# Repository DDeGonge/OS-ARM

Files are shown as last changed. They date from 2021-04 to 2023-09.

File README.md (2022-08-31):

# OS-ARM
An open-sourced, low cost, high performance 3D printed 6-axis robotic arm. The main goals of this project are
- Smooth, repeatable motion
- ~1kg payload
- ~500mm range
- Low cost (<$500 in materials)
- Easy to reproduce (only requiring an FDM printer and basic hand tools)
- Beautiful
- Easy to control

This arm is not industrial and it will not be fast, but that is not my goal. But it will hopefully be a very nice looking arm fully capable of 6dof motion, cheap enough to keep it accessable but capable enough to actually do something (aka carry more than a 50g payload). This is not your typical RC servo arm. It's gonna be epic.

Developemnt will likely take multiple years. This repo will be a work in progress until stated otherwise. Use these files at your own risk!

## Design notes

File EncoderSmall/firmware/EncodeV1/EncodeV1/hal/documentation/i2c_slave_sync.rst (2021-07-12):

============================
I2C Slave synchronous driver
============================

I2C (Inter-Integrated Circuit) is a two wire serial interface commonly used
for on-board low-speed bi-directional communication between controllers and
peripherals. There can be several slave devices on I2C bus.
I2C uses only two bidirectional open-drain lines, usually designated SDA
(Serial Data Line) and SCL (Serial Clock Line), with pull up resistors.

I2C Modes (standard mode/fastmode+/highspeed mode) can only be selected in
Atmel Start.

Features
--------

	* I2C Slave support
	* Initialization and de-initialization
	* Enabling and disabling
	* 10- and 7- bit addressing
	* Setting slave address
	* I2C Modes supported
	       +----------------------+-------------------+
	       |* Standard/Fast mode  | (SCL: 1 - 100kHz) |
	       +----------------------+-------------------+
	       |* Fastmode+           | (SCL: 1 - 1000kHz)|
	       +----------------------+-------------------+
	       |* Highspeed mode      | (SCL: 1 - 3400kHz)|
	       +----------------------+-------------------+

Applications
------------

* Sensors, device to device communication, memory.

Dependencies
------------

* I2C Slave capable hardware

Concurrency
-----------

N/A

Limitations
-----------

* System Management Bus (SMBus) not supported.
* Power Management Bus (PMBus) not supported.

Known issues and workarounds
----------------------------

N/A

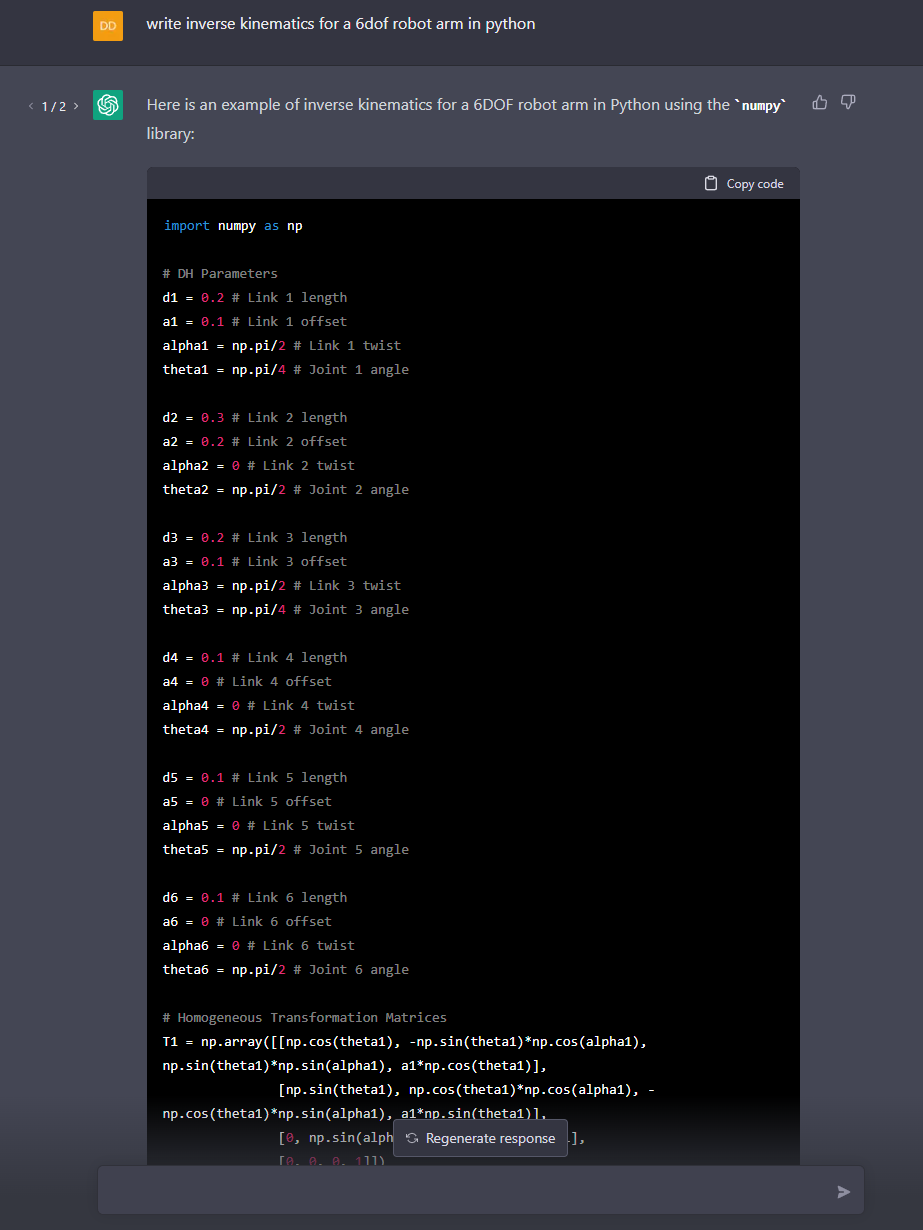
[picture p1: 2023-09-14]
firmware/chatgpt.png

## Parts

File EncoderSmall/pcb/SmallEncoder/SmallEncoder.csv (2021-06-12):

Id | Designator | Package | Quantity | Designation | Supplier and ref
1 | J3 | PinHeader_1x05_P2.54mm_Vertical | 1 | Conn_01x05
2 | C5,C4,C3 | C_0603_1608Metric | 3 | 100nF
3 | H3,H2,H1 | MountingHole_2.7mm_M2.5_DIN965_Pad | 3 | MountingHole_Pad
4 | R2 | R_0603_1608Metric | 1 | 174
5 | R1 | R_0603_1608Metric | 1 | 10k
6 | C2 | C_0603_1608Metric | 1 | 1uF
7 | C1 | C_0805_2012Metric | 1 | 10uF
8 | U3 | SOT-96-1 | 1 | KMZ49
9 | J2,J1 | PinHeader_1x04_P2.54mm_Horizontal | 2 | Conn_01x04
10 | U2 | SOT-23-5 | 1 | AP2112K-3.3
11 | S1 | KMR421GULCLFS | 1 | KMR243GLFG
12 | IC1 | QFN50P500X500X100-33N-D | 1 | ATSAMD21E15B

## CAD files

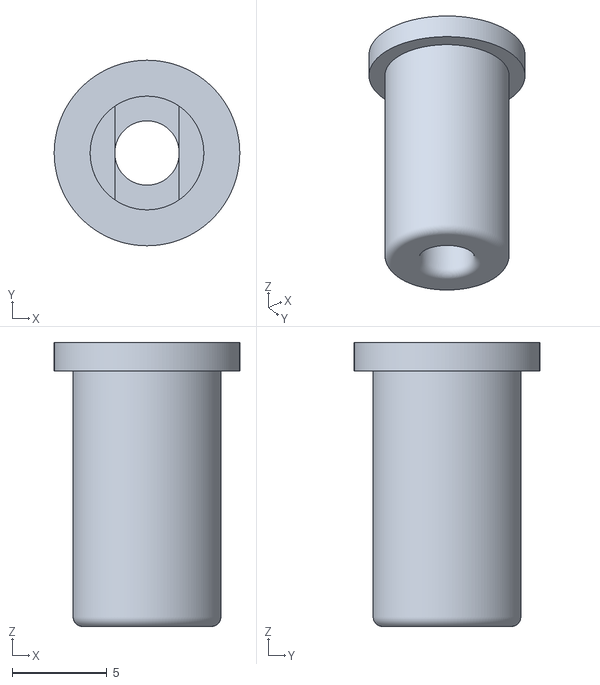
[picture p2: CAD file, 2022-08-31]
cad/HarmonicDrive75mm V2/HD_BearingShaft2.stl
9.80 x 9.80 x 15.0

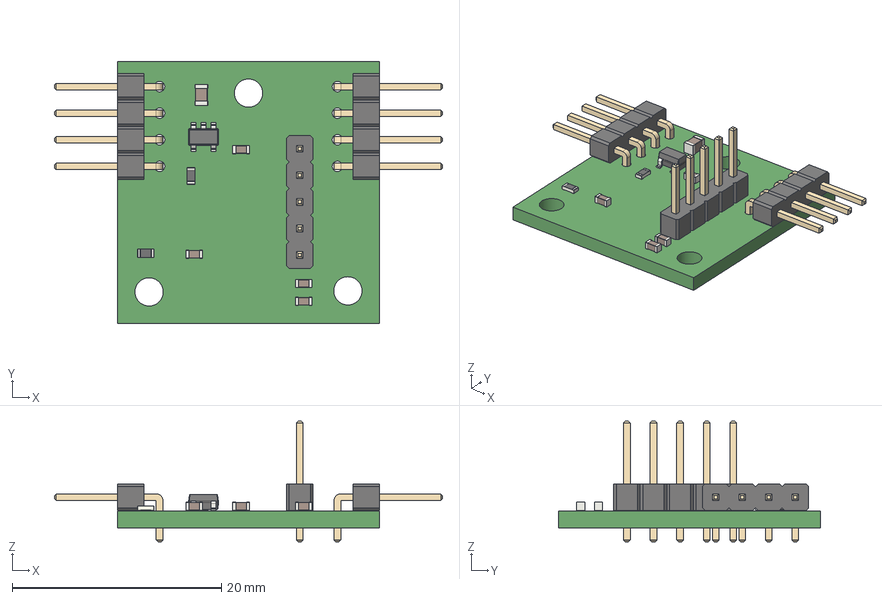
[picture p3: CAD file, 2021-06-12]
EncoderSmall/pcb/SmallEncoder/SmallEncoder.step
37.1 x 25.0 x 11.5 mm

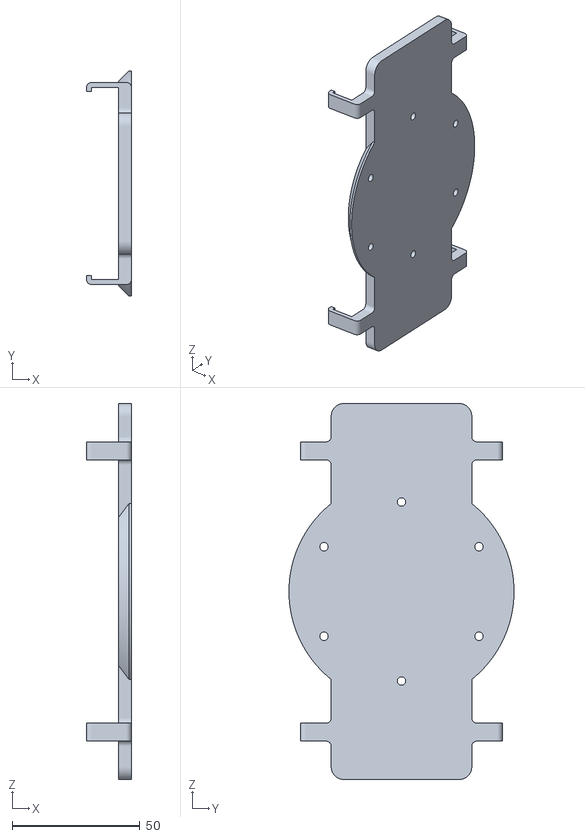
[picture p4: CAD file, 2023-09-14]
cad/FirstDraft/PhoneHOldER.stl
17.6 x 88.0 x 147.0

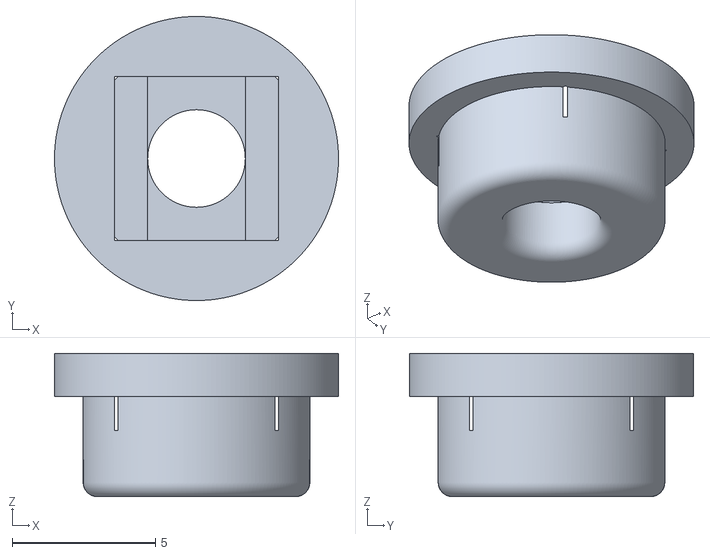
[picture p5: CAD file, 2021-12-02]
cad/HarmonicDrive75mm V2/HD_BearingShaft1.stl
9.90 x 9.90 x 5.00

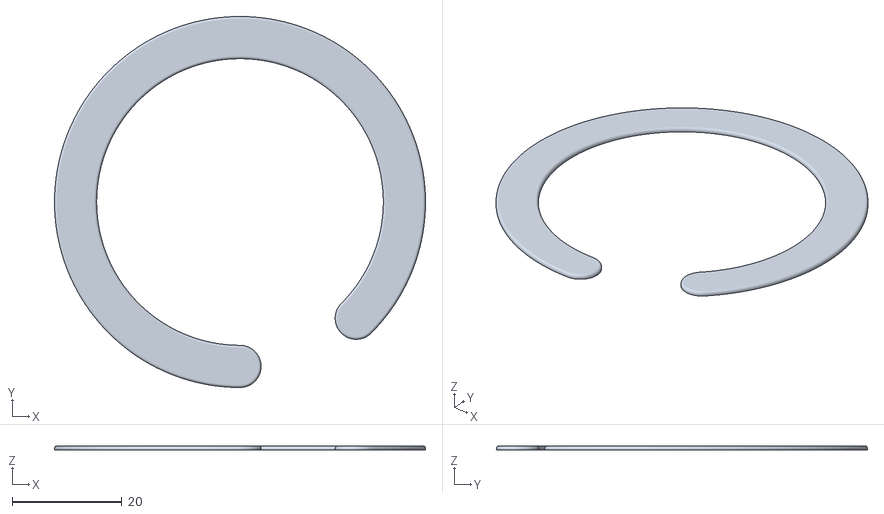
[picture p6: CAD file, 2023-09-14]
cad/FirstDraft/LogoCoverThin.stl
67.7 x 67.7 x 0.8

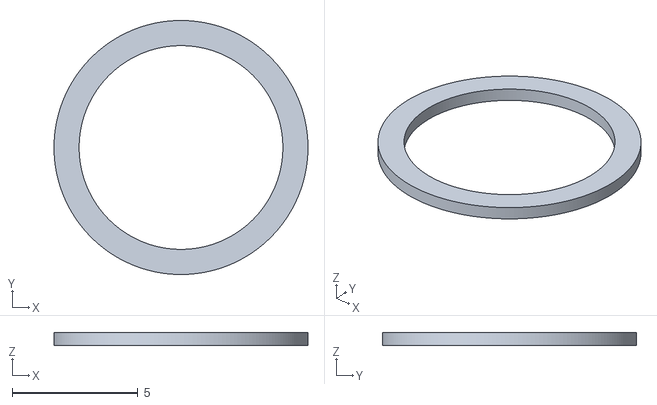
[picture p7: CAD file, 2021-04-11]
cad/HarmonicDrive75mm V2/HD_bearingshim.stl
10.1 x 10.1 x 0.5

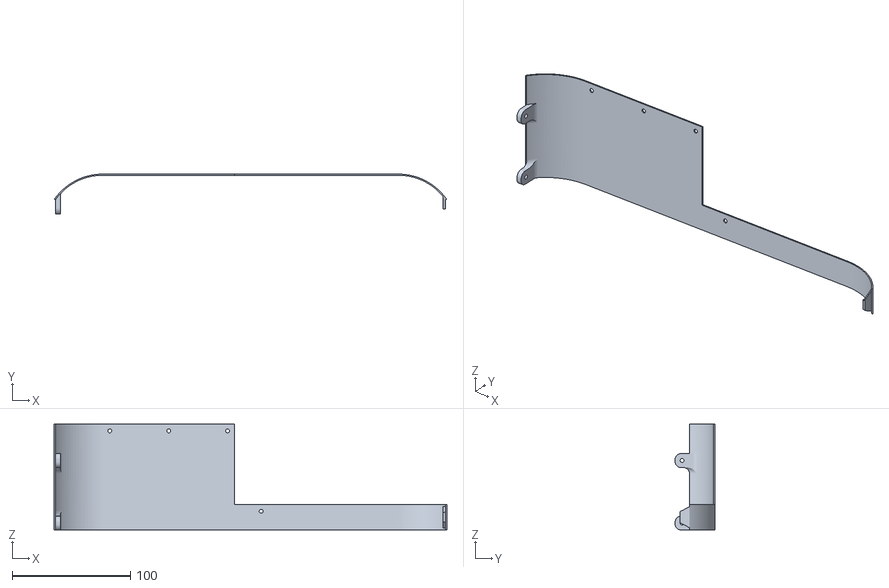
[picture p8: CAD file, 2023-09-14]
cad/FirstDraft/Link1CoverA.stl
332.4 x 33.7 x 89.6

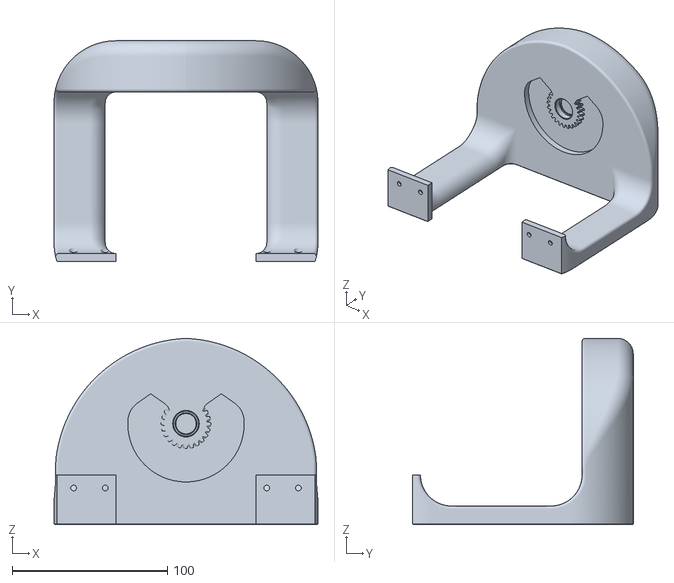
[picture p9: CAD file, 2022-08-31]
cad/FirstDraft/J1_NewBase.stl
170.0 x 142.0 x 119.9

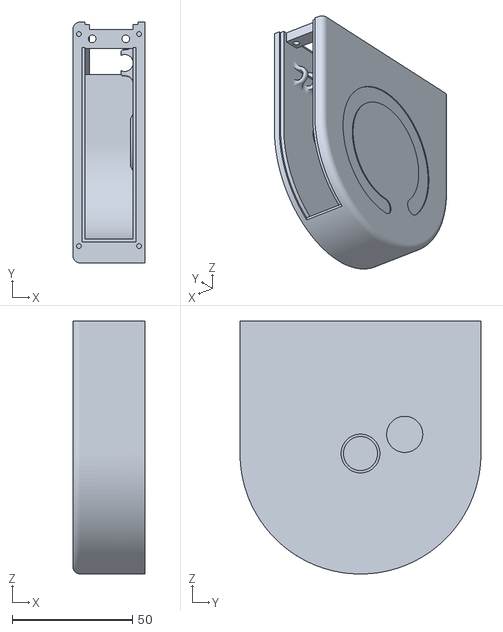
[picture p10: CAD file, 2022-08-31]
cad/FirstDraft/Link1c.stl
30.0 x 100.0 x 105.0

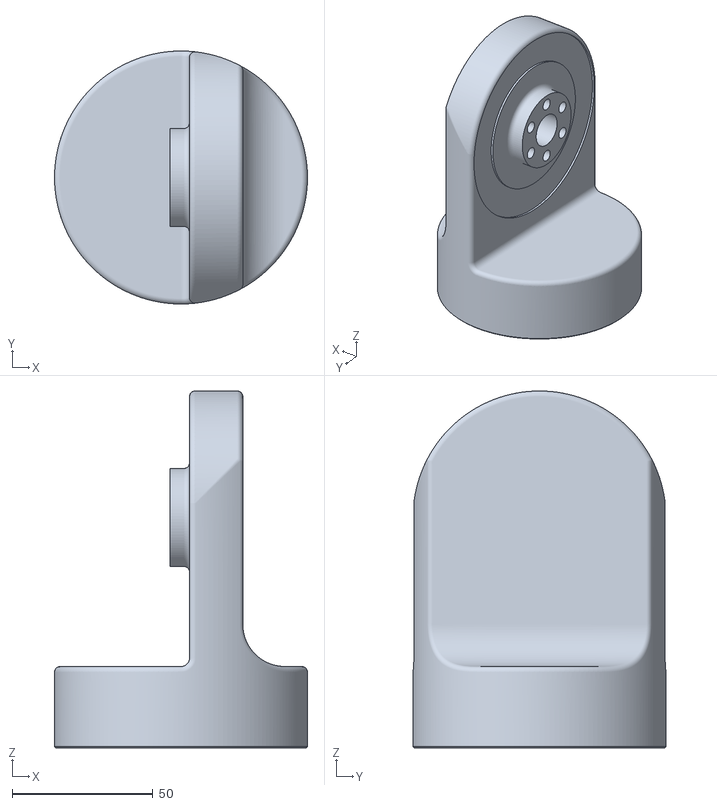
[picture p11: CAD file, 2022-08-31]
cad/FirstDraft/Link3.stl
90.0 x 90.0 x 127.0

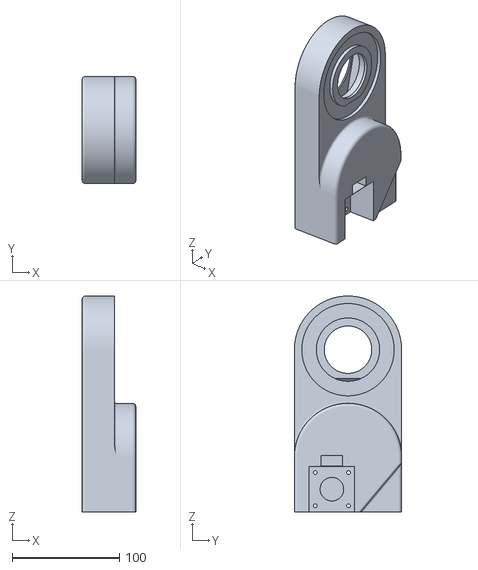
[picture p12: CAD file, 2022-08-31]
cad/FirstDraft/Link2B.stl
50.0 x 100.0 x 201.2

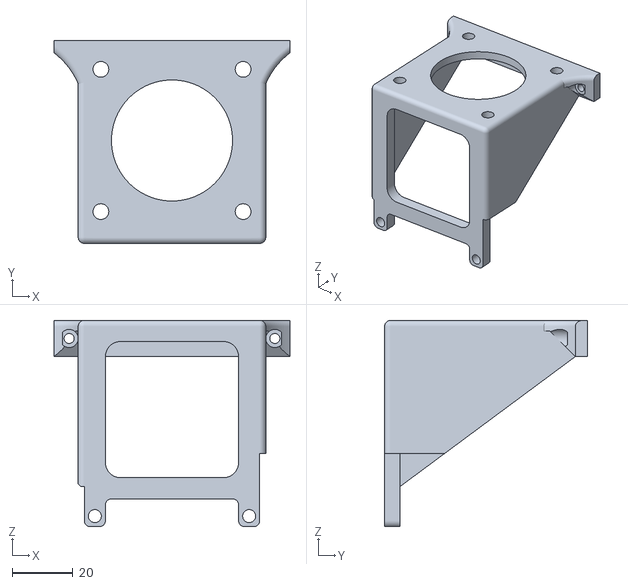
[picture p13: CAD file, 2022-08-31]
cad/FirstDraft/J2MotorBracket.stl
78.0 x 67.0 x 68.2

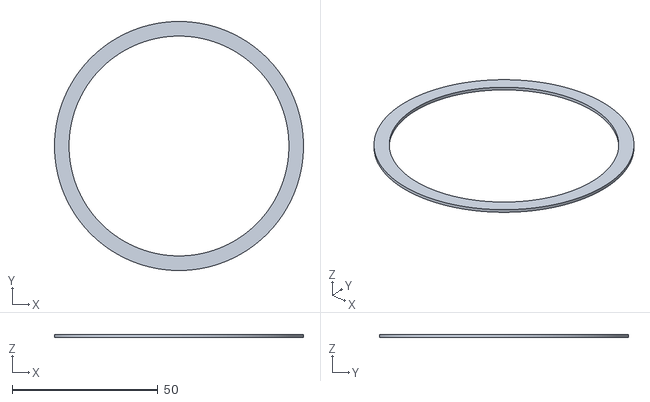
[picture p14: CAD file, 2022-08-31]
cad/FirstDraft/HDSpacer.stl
85.3 x 85.3 x 1.00

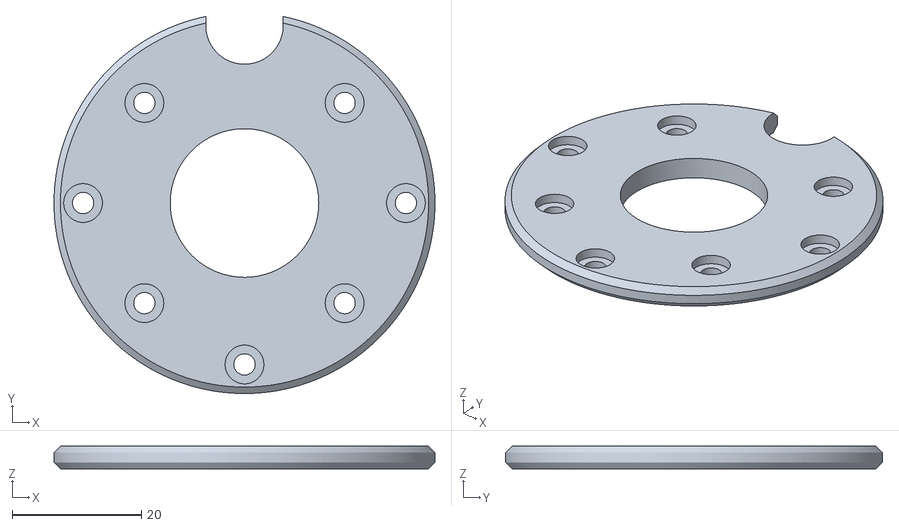
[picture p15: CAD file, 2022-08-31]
cad/FirstDraft/WristMotorPlate.stl
59.0 x 58.4 x 3.50

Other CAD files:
cad/FirstDraft/Link2_SpinCover.stl
cad/FirstDraft/Link2_FlatCover.stl
cad/FirstDraft/LogoCover.stl
cad/FirstDraft/TrainingTarget.stl
cad/FirstDraft/Base.ipt
cad/FirstDraft/Base.stl
cad/FirstDraft/BaseWasher.ipt
cad/FirstDraft/BaseWasher.stl
cad/FirstDraft/CamBracket.ipt
cad/FirstDraft/CamMount.ipt
cad/FirstDraft/Deskcap.ipt
cad/FirstDraft/Deskcap.stl
cad/FirstDraft/DraftAssembly.iam
cad/FirstDraft/DraftAssembly/Design Accelerator/OldVersions/Spur Gears1.0001.iam
cad/FirstDraft/DraftAssembly/Design Accelerator/OldVersions/Spur Gears2.0001.iam
cad/FirstDraft/DraftAssembly/Design Accelerator/Spur Gear21.ipt
cad/FirstDraft/DraftAssembly/Design Accelerator/Spur Gears1.iam
cad/FirstDraft/DraftAssembly/Design Accelerator/Spur Gears2.iam
cad/FirstDraft/EncoderSketch.ipt
cad/FirstDraft/EncoderV1/COMPOUND.ipt
cad/FirstDraft/EncoderV1/C_0603_1608Metric.iam
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

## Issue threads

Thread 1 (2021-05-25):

Slicer parameters and print material

3mrrrx, 2021-05-25:
Kindly add some information about the used slicer and parameters as well as the material that could be used for each part in read me.

DDeGonge, 2021-06-05:
Slicing and material is entirely up to you. I used PLA, PETG or ABS would likely offer slightly better performance, nylon the best. 30% or higher infill should be ok.

Closed 2021-06-05.

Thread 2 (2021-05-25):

bill of materials for the non-3D printed parts

3mrrrx, 2021-05-25:
bill of materials for the non-3D printed parts would be very very very very helpful recreate and try the project.

thank you!

DDeGonge, 2021-06-05:
I'll be filling in the BOM as I work on the project, apologies for the delay. The harmonic drive uses 608 and 688 bearings, plus some M3 square nuts and M3 bolts (I believe 20mm length for the bearing posts). But I will be uploading a full BOM in the next few weeks!

jlogan223, 2023-02-26:
Is there any update on this?

DDeGonge, 2023-03-10:
> Is there any update on this?

Hey sorry about that. I'm currently reworking the design from scratch so this design of the full arm is frozen. I plan to have a full BOM with the redesign which will be in Onshape so it is more accessible. But I don't have any idea of the full BOM for this iteration so if you want to build any part of it, you will need to open the cad and work out fasteners from that. Bearings are already included. And some heat stake inserts are used in the larger shallow holes where there's a screw but no obvious nut.

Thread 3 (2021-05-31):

lever at power off

michael-thompson-32214, 2021-05-31:
curious.
when the power is turned off.
does the lever arm rotate clock wise or counter clock wise easily

DDeGonge, 2021-06-05:
It does not, strain wave gearboxes usually can not be back-driven. This gearbox will hold its position when it is powered off.

Closed 2021-06-05.

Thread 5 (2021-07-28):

what program is required to edit the files?

bryanerayner, 2021-07-28:
Novice question here - what program is required to edit these files? Are there any free / freemium programs which would allow access?

Not asking you to change the way you work - thanks so much for opening this up! But a simple programmer like myself with no CAD experience would just like to know how to cut his teeth.

Thanks!

DDeGonge, 2021-08-01:
Autodesk Inventor is required to access the source files, though I have uploaded STEP files for the harmonic drive assembly and will for the full arm once it is in a stable place. STEP files can be opened and edited by most cad programs including some free ones, though editing features is not as easy as using Autodesk Inventor.

Closed 2021-08-01.

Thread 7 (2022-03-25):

Motor coupling missing?

Eufrades, 2022-03-25:
Hello DDeGonge,
I like the design of your 75mm harmonic drive, and I want to use it to drive a sand feeder for my sand spreader on the back of my garden tractor.
I printed all of the .stl parts from the V2 folder, but the wave generator is not the same as the one in your video, its obviously a newer version. There appears to be a coupling of some sort that goes between the wave generator and the motor. I've looked to see if I have missed a file, but I can't find it. Is that hiding somewhere?

Thanks for all of your work,
Eufrades

gandrewstone, 2022-03-28:
I think its meant to take a 20T GT2 timing belt pulley with the top flange popped off (based on a comment to the video here: https://www.youtube.com/watch?v=Emvo3bLT-Z4&t=16s).  I've got a stepper out of an old epson printer with a pulley that seems to match the wave generator... except I'm not sure because not sure how to pop the top flange off (blowtorch maybe?)

Since you are active, I have a question for you... have you figured out how the top housing is secured?  Seems to me like it would just fall off

gandrewstone, 2022-03-29:
Thats a good thought about the large bearing.  I bought one so in a few days I'll be able to tell.  That probably won't work for me either.  I was thinking of using it for a SCARA robot, so there will be force parallel to the motor shaft.  Maybe a stationary lid with a thrust bearing between will work for me, or something through the axle... What is your application?

Anyway the gear i had didnt actually fit, off by 2mm, so i made a bigger hole.  I also had elephant feet on my flex spline, so i fixed that by raising the teeth a tiny bit off the bed and printing with no supports.  I also put the skirt on the inside only.  I can give you the bkender models if you want.

gandrewstone, 2022-03-29:
What about the 688 bearings?  I think that they were originally on the motor shaft, but are not needed in the V2 design.

Eufrades, 2022-03-29:
I think you're right on the bearings, it doesn't look like they're needed anymore. As long ans the motor is mounted solidly to the bottom housing.
My application isn't typical for this type of gearbox, I just needed something with a really big speed reduction in a small package. I'm planning to use it on a sand spreader on the back of my atv. There is a motor there that already spins the spreader, but I wanted to use the same motor to really slowly turn an agitator in the sand hopper because the sand keeps getting hung up in there.
I appreciate the offer of your files, but I think I'm going to modify this quite a bit more to slow it down even more for me.

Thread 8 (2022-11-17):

Reduction ratio

Okosai, 2022-11-17:
So, i am modifying v2 harmonic drive (for my motorised telescope mount) and i am trying to figure out what is actual rediction ratio for it. As far as i understood one of the rings has 70 teeth and 68 another, meanwhile spline has 66 teeth... could not find any info on that.
Thanks

KoehIl180151, 2023-01-27:
I would also need this information.
I tried to calculate it myself with the steps per rev and i got 1:29 but in testing it didn't quite work out.

bfra2373, 2023-01-27:
Looking at [wiki](https://en.wikipedia.org/wiki/Strain_wave_gearing) You should see that the  ratio is
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
or For example, if there are 202 teeth on the circular spline and 200 on the flex spline, the reduction ratio is (200 − 202)/200 = −0.01

DDeGonge, 2023-01-27:
Because my harmonic drive is designed different than the standard, the formula above needs slight modification.

The number of teeth in my "flex spline" is irrelevant, instead what matters is the number of teeth on the input (circle spline equivalent) vs output (flex spline equivalent) sides of the housing. So the formula would be (68 - 70) / 68, which gives a reduction of **34:1**. Note this equation results in a negative number, which means the output spins the opposite direction of the input.

Closed 2023-01-27.

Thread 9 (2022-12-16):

Export to other cad formats

bit-wrangler, 2022-12-16:
Hey, do you mind exporting the gearbox design to solidworks or STEP? I guess I'm working with some pretty old CAD as it's erroring out trying to import the ipt/iam files.

DDeGonge, 2023-09-14:
Apologies for not seeing this sooner, done now

Closed 2023-09-14.

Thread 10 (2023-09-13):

Different Modules Gear Meshing

Archav, 2023-09-13:
Can someone explain how the gears mesh? I'm currently working on my own harmonic drive with different gear ratio and am using this as a reference on how to go about printing it.
Looking at the CAD files the ring gear and the flex spline have 70 and 68 teeth. When creating the gear in Inventors Spur Gear generator there is too much overlap in teeth to allow the flex spline to mesh. This design seems to be using two different gear modules to create more of a gap. has anyone encountered any issues with gear meshing or tips to know while printing?
Thanks in advance.

DDeGonge, 2023-09-14:
The teeth were designed from scratch in my design, and the tooth was patterned 2 additional times over the same circumference. You may not be able to do this if you're using a script or add-on to generate the gear teeth. Additionally, the standard involute gear profile is probably not the optimal shape for this time of gearbox. So making teeth from scratch would give more room for improving efficiency and thus power output.

Closed 2023-09-14.

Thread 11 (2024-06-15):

Printer Material and Settings

cmagorian, 2024-06-15:
Hey! Nice work on this, just found your video which brought me back here.

What print settings did you use across all the parts? Did you use a different filament for the FlexiSpine? If so, which one?

Thanks!
Chris

DDeGonge, 2025-02-11:
Sorry late reply - I used PLA but would recommend PETG be used for the flex spline. More tensile strength is generally better (hence PLA) but the flex spline needs better fatigue resistance. CF filled may help too but those plastics are more abrasive so lifetime might be reduced. I haven't tried using nylon filament but I suspect that would work very well for the flex spline as well. It may be too soft for the entire gearbox though depending on the blend.

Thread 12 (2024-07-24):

Upload SPT of the entire OS-ARM First Draft

cmagorian, 2024-07-24:
Hey!

Started using this at my own risk. I am mostly interested in just building out parts of the arm for 4DOF: Waist, Shoulder, Elbow and Wrist (1 DOF). Any way you could upload an STP of the First Draft assembly? The parts are in here, but I don't see the thing put together. Those of us using Onshape can't import the IAM files.

Thanks!
Chris

DDeGonge, 2024-07-25:
Added under cad/FirstDraft/DraftAssembly.step

Closed 2024-07-25.

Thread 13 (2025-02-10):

Likely limitation to achieve 2x torque

spit40, 2025-02-10:
I have a motion platform for flight simulation. The motors are terrible though. They are windscreen wiper worm drives with loads of backlash. I’m thinking that a 3d printed strainwave motor could be the solution. It hink i’d need 2x to 3x torque though but am concerned that a stronger motor would simply result in mechanical failure probably on the toothed belt. Has anyone else tried to scale this up in torque?

DDeGonge, 2025-02-11:
I would definitely not recommend a 3D printed gearbox for loads that high. While this gearbox could probably operate at up to a 20Nm output, I have some hesitation about the lifetime. Even at 10Nm I wouldn't be surprised to start seeing fatigue failures after a few weeks under these loads.

If you need linear motion, using a cheap ball screw with a geared down input from a motor using a belt reduction would be a reliable way to hit very high output forces. If you need rotation, an off the shelf solution would be expensive but if you want it to last any amount of time it's either that, or likely a whole lot of engineering and trials before you hit a reliable solution.

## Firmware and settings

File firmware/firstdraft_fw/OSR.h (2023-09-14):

#include <Arduino.h>
#include <SPI.h>
#include <vector>
#include <iostream>

#define NOVALUE 999999


/* Stepper driver object, to be used with up to 2 stepper objects */
struct TMC2041
{
    TMC2041() {};
    TMC2041(uint8_t en_pin, uint8_t cs_pin);
    TMC2041(uint8_t en_pin, uint8_t cs_pin, bool single_motor_mode);

    public:
    void set_pins(uint8_t en_pin, uint8_t cs_pin);
    void configure();
    void enable_driver();
    void disable_driver();

    /* Driver com functions */
    void write_gconf();
    uint8_t get_ihold_address(uint8_t index);
    uint8_t get_chop_address(uint8_t index);
    uint8_t get_cool_address(uint8_t index);
    uint8_t get_status_address(uint8_t index);
    void write_cmd(uint8_t addr, uint8_t chunk[4]);
    int32_t read_cmd(uint8_t addr);

    private:
    uint8_t EN_PIN;
    uint8_t CS_PIN;

    /* SPI functions */
    SPISettings TMCspiSettings = SPISettings(1000000, MSBFIRST, SPI_MODE3); 
    
    /* Addresses. Tuple if unique address for each stepper */
    uint8_t a_gconf = 0x00;
    uint8_t a_iholdirun[2] = {0x30, 0x50};
    uint8_t a_chop[2] = {0x6C, 0x7C};
    uint8_t a_cool[2] = {0x6D, 0x7D};
    uint8_t a_status[2] = {0x6F, 0x7F};

    /* Driver level bitfields */
    uint8_t gconf[4] = {B00000000, B00000000, B00000000, B00000110};
};

/* Stepper driver object */
struct TMC5160
{
    TMC5160() {};
    TMC5160(uint8_t en_pin, uint8_t cs_pin);

    public:
    void set_pins(uint8_t en_pin, uint8_t cs_pin);
    void configure();
    void enable_driver();
    void disable_driver();

    /* Driver com functions */
    void write_gconf();
    uint8_t get_ihold_address();
    uint8_t get_chop_address();
    uint8_t get_cool_address();
    uint8_t get_status_address();
    uint8_t get_gstat_address();
    uint8_t get_tpowerdown_address();
    uint8_t get_tpwmthrs_address();
    void write_cmd(uint8_t addr, uint8_t chunk[4]);
    int32_t read_cmd(uint8_t addr);

    private:
    uint8_t EN_PIN;
    uint8_t CS_PIN;

    /* SPI functions */
    SPISettings TMCspiSettings = SPISettings(1000000, MSBFIRST, SPI_MODE3); 
    
    /* SPI Addresses. Tuple if unique address for each stepper */
    uint8_t a_gconf = 0x00;
    uint8_t a_gstat = 0x01;
    uint8_t a_ioin = 0x04;
    uint8_t a_sconf = 0x09;
    uint8_t a_drvconf = 0x0A;
    uint8_t a_drvcur = 0x0B;
    uint8_t a_iholdirun = 0x10;
    uint8_t a_chop = 0x6C;
    uint8_t a_cool = 0x6D;
    uint8_t a_status = 0x6F;
    uint8_t a_tpowerdown = 0x11;
    uint8_t a_tpwmthrs = 0x13;

    /* SPI default bitfields */
    // uint8_t gconf[4] = {B00000000, B00000000, B00000000, B00001100};
    uint8_t gconf[4] = {B00000000, B00000000, B00000000, B00001000};  // take3
};

/* Stepper object, supports 2041 and 5160 driver types */
struct TMCstep
{
    TMCstep() {};
    TMCstep(uint8_t step_pin, uint8_t dir_pin, TMC2041 &my_driver, uint8_t motor_index, bool reverse = false);
    TMCstep(uint8_t step_pin, uint8_t dir_pin, TMC5160 &my_driver, bool reverse = false);

    public:
    uint8_t drv_type = 0;
    TMC2041 driver_2041;  // Type 1
    TMC5160 driver_5160;  // Type 2

    void set_2041_default_bitfields();
    void set_5160_default_bitfields();

    void set_pins(uint8_t step_pin, uint8_t dir_pin);
    void set_index(uint8_t index);
    uint8_t get_index();

    void step();
    void set_step(int32_t steps);
    int32_t get_step();
    void set_dir(bool dir);
    bool get_dir();

    void enable();
    void disable();

    /* Motor configurating funcs */
    void set_hold_current(uint8_t newval); // Values 0-31 acceptable
    void set_run_current(uint8_t newval);  // Values 0-31 acceptable
    void set_microsteps(uint8_t newval);   // Values 0 (256u) to 8 (fullstep) acceptable

    /* Driver com functions */
    void write_iholdirun();
    void write_chop();
    void write_cool();
    void update_motor_status();
    uint32_t debug_print_status();

    /* Sensorless homing stuff */
    bool get_stallguard();
    uint32_t get_stall_value();

    /* Motor level bitfields */
    // TODO these should probably be private
    uint8_t ihold[4] = {B00000000, B00000001, B00010000, B00001000};
    uint8_t chop[4]  = {B00000010, B00000001, B00000000, B00000011};
    uint8_t cool[4]  = {B00000000, B00000110, B00000000, B00000000};
    uint8_t saved_chop = chop[3];


    private:
    uint8_t INDEX;
    uint8_t STEP_PIN;
    uint8_t DIR_PIN;
    uint16_t step_pulse_len_us = 1;
    bool reversed = false;

    int32_t step_count = 0;
    bool motor_dir = false;

    uint32_t status_bits;

    void clear_bits(uint8_t &chunk, uint8_t i_min, uint8_t i_max);
    void write_bits(uint8_t &chunk, uint8_t new_chunk, uint8_t i_min, uint8_t i_max);
};

/* Stepper motor wrapper to handle motion profiles */
// TODO simplify this and merge with TMCstep
struct motorDrive
{
    motorDrive(TMCstep &new_stepper, int32_t steps_per_mm_new);

    public:
    // Configuration functions
    void set_default_vel_mmps(float max_vel_new);
    void set_default_acc_mmps2(float max_accel_new);
    void set_steps_per_mm(int32_t steps_per_mm_new);

    // Zeroing & Other Functions
    void set_current_pos_mm(double target);
    void zero();
    void enable();
    void disable();
    void set_move_limits_mm(float minlim, float maxlim);
    double get_current_pos_mm();
    double get_current_vel_mmps();

    // Homing and sensing related
    void home(bool to_min = true);
    uint32_t get_stall_value();

    // Async move related supporting real time target adjustment. Limit of ~20KHz step speed
    void set_pos_target_mm_async(double target, float feedrate = NOVALUE);
    bool step_if_needed(uint32_t t_now = micros());
    
    // Standard Synchronous move
    void set_pos_target_mm_sync(double target, float feedrate = NOVALUE, bool ignore_limits = false);
    
    // Pre-planned async move. Runs WAY faster than the realtime version
    void plan_move(double target, float feedrate = NOVALUE, float accel = NOVALUE, bool ignore_limits = false);
    void execute_move_async();
    bool async_move_step_check(uint32_t t_now = micros(), bool stall_check = false);


    private:
    TMCstep stepper;

    // Configuration
    float steps_per_mm = 160;
    float max_vel = 100;
    float home_vel = 30;
    float max_accel = 500;
    float min_dist_mm = -10000;
    float max_dist_mm = 10000;
    float home_backoff_mm = 1;
    float step_size_mm;

    // Backend funcs
    void quad_solve(double &t_0, double &t_1, double a, double b, double c);
    int32_t solve_for_t_us(float v, float a, float d);
    double check_target(double target);

    // Control vars
    double target_mm = 0;

    // Async Motion tracking vars
    bool stopped = true;
    double current_velocity = 0;
    double diff_exact_us = 0;
    uint32_t last_step_us = 0;
    uint32_t next_step_us = 0;

    // Sync motion tracking vars
    int8_t plan_sign;
    int32_t plan_tmin;
    uint32_t plan_asteps = 0;;
    uint32_t plan_nsteps = 0;;
    std::vector<uint16_t> plan_accel_timings;

    uint32_t plan_stepstaken = 0;
    uint32_t plan_nextstep_us = 0;
};

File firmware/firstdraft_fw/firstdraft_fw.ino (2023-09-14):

#include "OSR.h"
#include "gparse.h"
#include "pins.h"

#define Serial SERIAL_PORT_USBVIRTUAL

void setup() {
  // put your setup code here, to run once:
  Serial.begin(250000);
  while (!Serial);
  Serial.println("BEGINNING!");

  delay(100);

  pinMode(LED_BUILTIN, OUTPUT);
  digitalWrite(LED_BUILTIN, HIGH);

//  pinMode(S1CS, OUTPUT);
//  pinMode(14, OUTPUT);
//  pinMode(15, OUTPUT);
//  while(true)
//  {
//    digitalWrite(S1CS, HIGH);
//    digitalWrite(14, HIGH);
//    digitalWrite(15, HIGH);
//    delay(1000);
//    digitalWrite(S1CS, LOW);
//    digitalWrite(14, LOW);
//    digitalWrite(15, LOW);
//    delay(1000);
//  }
}

void loop() {
  uint8_t clear_faults[4] = {B00000000, B00000000, B00000000, B00000111};  // write this to 0x01 to clear driver faults
  
  /* Stepper drive initialization */
  TMC5160 Driver0(S0EN, S0CS);
  TMCstep Stepper0 = TMCstep(S0STEP, S0DIR, Driver0, false);
  Serial.println("Driver 0 initialized...");
  
  TMC5160 Driver1(S1EN, S1CS);
  TMCstep Stepper1 = TMCstep(S1STEP, S1DIR, Driver1, false);
  Serial.println("Driver 1 initialized...");
  
  TMC5160 Driver2(S2EN, S2CS);
  TMCstep Stepper2 = TMCstep(S2STEP, S2DIR, Driver2, true);
  Serial.println("Driver 2 initialized...");
  
  TMC2041 Driver3(S3S4EN, S3S4CS);
  TMCstep Stepper3 = TMCstep(S3STEP, S3DIR, Driver3, 0, false);
  TMCstep Stepper4 = TMCstep(S4STEP, S4DIR, Driver3, 1, false);
  Serial.println("Driver 3/4 initialized...");
  
  TMC2041 Driver5(S5S6EN, S5S6CS);
  TMCstep Stepper5 = TMCstep(S5STEP, S5DIR, Driver5, 0, false);
  TMCstep Stepper6 = TMCstep(S6STEP, S6DIR, Driver5, 1, false);
  Serial.println("Driver 5/6 initialized...");

  /* Stepper drive configuration */
  Serial.println("Configuring motor drivers...");
  Driver0.configure();
  Driver1.configure();
  Driver2.configure();
  Driver3.configure();
  Driver5.configure();
  Serial.println("Configured motor drivers");

  motorDrive mDrive0 = motorDrive(Stepper0, 3050);   // steps per rad
  motorDrive mDrive1 = motorDrive(Stepper1, 12987); // steps per rad, 102:1 reduction  - 103896
  motorDrive mDrive2 = motorDrive(Stepper2, 12987); // steps per rad, 102:1 reduction
  motorDrive mDrive3 = motorDrive(Stepper3, 10695);  // steps per rad 8:1 reduction - 10695
  motorDrive mDrive4 = motorDrive(Stepper4, 6400);   // steps per rad,
  motorDrive mDrive5 = motorDrive(Stepper5, 6400);   // steps per rad
  motorDrive mDrive6 = motorDrive(Stepper6, 6400);   // steps per rad

  Stepper0.set_run_current(29);
  Stepper0.set_hold_current(12);
  Stepper0.set_microsteps(4); // 1/16 stepping
  mDrive0.set_default_vel_mmps(1);
  mDrive0.set_default_acc_mmps2(20);
  mDrive0.set_move_limits_mm(-1.65, 1.65);

  Stepper1.set_run_current(30);
  Stepper1.set_hold_current(12);
  Stepper1.set_microsteps(6); // 1/4 stepping
  mDrive1.set_default_vel_mmps(0.5);
  mDrive1.set_default_acc_mmps2(5);
  mDrive0.set_move_limits_mm(0.0, 2.25);

  Stepper2.set_run_current(30);
  Stepper2.set_hold_current(12);
  Stepper2.set_microsteps(6); // 1/4 stepping
  mDrive2.set_default_vel_mmps(0.5);
  mDrive2.set_default_acc_mmps2(5);
  mDrive0.set_move_limits_mm(0.0, 2.25);

  Stepper3.set_run_current(30);
  Stepper3.set_hold_current(26);
  Stepper0.set_microsteps(4); // 1/16 stepping
  mDrive3.set_default_vel_mmps(1.0);
  mDrive3.set_default_acc_mmps2(25);
  mDrive3.set_move_limits_mm(-1.7, 1.7);

  Stepper4.set_run_current(28);
  Stepper4.set_hold_current(20);
  mDrive4.set_default_vel_mmps(1);
  mDrive4.set_default_acc_mmps2(50);
  mDrive4.set_move_limits_mm(0.0, 2.25);

  Stepper5.set_run_current(28);
  Stepper5.set_hold_current(20);
  mDrive5.set_default_vel_mmps(1);
  mDrive5.set_default_acc_mmps2(50);
  mDrive5.set_move_limits_mm(0.0, 2.25);

  Stepper6.set_run_current(28);
  Stepper6.set_hold_current(24);
  mDrive6.set_default_vel_mmps(0.5);
  mDrive6.set_default_acc_mmps2(25);
  mDrive6.set_move_limits_mm(-6.5, 6.5);

  Serial.println("Enabling and zeroing all motors");
  mDrive0.enable();
  mDrive1.enable();
  mDrive2.enable();
  mDrive3.enable();
  mDrive4.enable();
  mDrive5.enable();
  mDrive6.enable();

  char serial_data[MAX_MSG_LEN];
  clear_data(serial_data);
  char base_cmd, char_value;
  int32_t base_value, int_value;
  float float_value;
  bool run_dynostep_loop = false;

//  while (true) 
//  {
//    Serial.println("Drive 0...");
//    mDrive0.set_pos_target_mm_sync(0.1, 300*1, false);
//    mDrive0.set_pos_target_mm_sync(0, 300*1, false);
//    Serial.println("Drive 1...");
//    mDrive1.set_pos_target_mm_sync(0.1, 10*1, true);
//    mDrive1.set_pos_target_mm_sync(0, 10*1, false);
//    Serial.println("Drive 2...");
//    mDrive2.set_pos_target_mm_sync(0.1, 10*1, false);
//    mDrive2.set_pos_target_mm_sync(0, 10*1, false);
//    Serial.println("Drive 3...");
//    mDrive3.set_pos_target_mm_sync(0.1, 200*1, false);
//    mDrive3.set_pos_target_mm_sync(0, 200*1, false);
////    Serial.println("Drive 4...");
////    mDrive4.set_pos_target_mm_sync(1, 60*1, false);
////    mDrive4.set_pos_target_mm_sync(0, 60*1, false);
////    Serial.println("Drive 5...");
////    mDrive5.set_pos_target_mm_sync(1, 120*1, false);
////    mDrive5.set_pos_target_mm_sync(0, 120*1, false);
//    Serial.println("Drive 6...");
//    mDrive6.set_pos_target_mm_sync(0.1, 600*1, false);
//    mDrive6.set_pos_target_mm_sync(0, 600*1, false);
//  }

//  speedtest(mDrive1, 0.3, 0.5, 2, 0.1);

  while (true)
  {
    // First handle the async step thing if you wanna go this route
    if (run_dynostep_loop)
    {
      uint32_t tnow = micros();
      bool r0 = mDrive0.step_if_needed(tnow);
      bool r1 = mDrive1.step_if_needed(tnow);
      bool r2 = mDrive2.step_if_needed(tnow);
      bool r3 = mDrive3.step_if_needed(tnow);
      bool r6 = mDrive6.step_if_needed(tnow);

      if (!r0 && !r1 && !r2 && !r3 && !r6)
      {
        Serial.println("STOPPING DYNOSTEPPS");
        run_dynostep_loop = false;
      }
    }
    

    if (respondToSerial(serial_data)) 
    {
      vector<string> args;
      parse_inputs(serial_data, args);
      parse_int(args[0], base_cmd, base_value);

      switch (tolower(base_cmd)) 
      {
        case 'g': {
          switch (base_value) 
          {
            case 0: {
              // LINEAR MOVE DO NOT WAIT
              gcode_command_floats gcode(args);
              if(gcode.com_exists('x')) mDrive0.set_pos_target_mm_async(gcode.fetch('x'), gcode.fetch('f'));
              if(gcode.com_exists('y')) mDrive1.set_pos_target_mm_async(gcode.fetch('y'), gcode.fetch('f'));
              if(gcode.com_exists('z')) mDrive2.set_pos_target_mm_async(gcode.fetch('z'), gcode.fetch('f'));
              if(gcode.com_exists('a')) mDrive3.set_pos_target_mm_async(gcode.fetch('a'), gcode.fetch('f'));
              if(gcode.com_exists('b')) mDrive6.set_pos_target_mm_async(gcode.fetch('b'), gcode.fetch('f'));
              run_dynostep_loop = true;
              break;
            }
            case 1: {
              // LINEAR MOVE WAIT
              gcode_command_floats gcode(args);
              if(gcode.com_exists('x')) mDrive0.plan_move(gcode.fetch('x'), gcode.fetch('f'));
              if(gcode.com_exists('y')) mDrive1.plan_move(gcode.fetch('y'), gcode.fetch('f'));
              if(gcode.com_exists('z')) mDrive2.plan_move(gcode.fetch('z'), gcode.fetch('f'));
              if(gcode.com_exists('a')) mDrive3.plan_move(gcode.fetch('a'), gcode.fetch('f'));
              if(gcode.com_exists('b')) mDrive6.plan_move(gcode.fetch('b'), gcode.fetch('f'));
//              if(gcode.com_exists('c')) mDrive5.plan_move(gcode.fetch('c'), gcode.fetch('f'));
              
              mDrive0.execute_move_async();
              mDrive1.execute_move_async();
              mDrive2.execute_move_async();
              mDrive3.execute_move_async();
              mDrive6.execute_move_async();
//              mDrive5.execute_move_async();
              while(true)
              {
                uint32_t tnow = micros();
                bool r0 = mDrive0.async_move_step_check(tnow);
                bool r1 = mDrive1.async_move_step_check(tnow);
                bool r2 = mDrive2.async_move_step_check(tnow);
                bool r3 = mDrive3.async_move_step_check(tnow);
                bool r6 = mDrive6.async_move_step_check(tnow);
//                bool r5 = mDrive5.async_move_step_check(tnow);
                if(r0 && r1 && r2 && r3 && r6)
                  break;
              }
              break;
            }
            case 92: {
              // Overwrite current pos
              gcode_command_floats gcode(args);
              if(gcode.com_exists('x')) mDrive0.set_current_pos_mm(gcode.fetch('x'));
              if(gcode.com_exists('y')) mDrive1.set_current_pos_mm(gcode.fetch('y'));
              if(gcode.com_exists('z')) mDrive2.set_current_pos_mm(gcode.fetch('z'));
              if(gcode.com_exists('a')) mDrive3.set_current_pos_mm(gcode.fetch('a'));
              if(gcode.com_exists('b')) mDrive6.set_current_pos_mm(gcode.fetch('b'));
//              if(gcode.com_exists('c')) mDrive5.set_current_pos_mm(gcode.fetch('c'));
              if(!gcode.com_exists('x') && !gcode.com_exists('y') && !gcode.com_exists('z') && !gcode.com_exists('a') && !gcode.com_exists('b')) // && !gcode.com_exists('c'))
              {
                mDrive0.zero();
                mDrive1.zero();
                mDrive2.zero();
                mDrive3.zero();
                mDrive6.zero();
//                mDrive5.zero();
              }
              break;
            }
            case 100: {
              // Overwrite default vel
              gcode_command_floats gcode(args);
              if(gcode.com_exists('x')) mDrive0.set_default_vel_mmps(gcode.fetch('x'));
              if(gcode.com_exists('y')) mDrive1.set_default_vel_mmps(gcode.fetch('y'));
              if(gcode.com_exists('z')) mDrive2.set_default_vel_mmps(gcode.fetch('z'));
              if(gcode.com_exists('a')) mDrive3.set_default_vel_mmps(gcode.fetch('a'));
              if(gcode.com_exists('b')) mDrive6.set_default_vel_mmps(gcode.fetch('b'));
//              if(gcode.com_exists('c')) mDrive5.set_default_vel_mmps(gcode.fetch('c'));
              break;
            }
            case 101: {
              // Overwrite default acc
              gcode_command_floats gcode(args);
              if(gcode.com_exists('x')) mDrive0.set_default_acc_mmps2(gcode.fetch('x'));
              if(gcode.com_exists('y')) mDrive1.set_default_acc_mmps2(gcode.fetch('y'));
              if(gcode.com_exists('z')) mDrive2.set_default_acc_mmps2(gcode.fetch('z'));
              if(gcode.com_exists('a')) mDrive3.set_default_acc_mmps2(gcode.fetch('a'));
              if(gcode.com_exists('b')) mDrive6.set_default_acc_mmps2(gcode.fetch('b'));
//              if(gcode.com_exists('c')) mDrive5.set_default_acc_mmps2(gcode.fetch('c'));
              break;
            }
          }
        }
        case 'm': {
          switch (base_value) 
          {
            case 80: {
              mDrive0.enable();
              mDrive1.enable();
              mDrive2.enable();
              mDrive3.enable();
              mDrive6.enable();
              break;
            }
            case 81: {
              mDrive0.disable();
              mDrive1.disable();
              mDrive2.disable();
              mDrive3.disable();
              mDrive6.disable();
              break;
            }
            case 114: {
              Serial.print("X:");
              Serial.print(mDrive0.get_current_pos_mm());
              Serial.print(" Y:");
              Serial.print(mDrive1.get_current_pos_mm());
              Serial.print(" Z:");
              Serial.print(mDrive2.get_current_pos_mm());
              Serial.print(" A:");
              Serial.print(mDrive3.get_current_pos_mm());
              Serial.print(" B:");
              Serial.print(mDrive6.get_current_pos_mm());
//              Serial.print(" C:");
//              Serial.print(mDrive0.get_current_pos_mm());
              Serial.println();
              break;
            }
          }
        }
        Serial.println("ok");
        clear_data(serial_data);
      }
    }
  }
  

  delay(200);
  int movetarget = 1;

//  speedtest(mDrive3, 20, 10, 20, 0.5);
//  speedtest(mDrive5, 0.5, 0.5, 2, 0.1);

//  while (true) 
//  {
//    mDrive3.set_pos_target_mm_sync(3, 60*5, false);
//    mDrive3.set_pos_target_mm_sync(0, 60*5, false);
//    mDrive5.set_pos_target_mm_sync(0.1, 60*0.5, false);
//    mDrive5.set_pos_target_mm_sync(0, 60*0.5, false);
//  }
}

void speedtest(motorDrive mDrive, float dist, float vstart, float vend, float vstep)
{
  for (float v = vstart; v < vend; v += vstep)
  {
    Serial.print("Setting speed to ");
    Serial.print(v);
    Serial.print(" rads/s\n");

    mDrive.set_pos_target_mm_sync(dist, 60*v, false);
    mDrive.set_pos_target_mm_sync(0, 60*v, false);
  }
}

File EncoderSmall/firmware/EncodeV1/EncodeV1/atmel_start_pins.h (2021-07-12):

/*
 * Code generated from Atmel Start.
 *
 * This file will be overwritten when reconfiguring your Atmel Start project.
 * Please copy examples or other code you want to keep to a separate file
 * to avoid losing it when reconfiguring.
 */
#ifndef ATMEL_START_PINS_H_INCLUDED
#define ATMEL_START_PINS_H_INCLUDED

#include <hal_gpio.h>

// SAMD21 has 8 pin functions

#define GPIO_PIN_FUNCTION_A 0
#define GPIO_PIN_FUNCTION_B 1
#define GPIO_PIN_FUNCTION_C 2
#define GPIO_PIN_FUNCTION_D 3
#define GPIO_PIN_FUNCTION_E 4
#define GPIO_PIN_FUNCTION_F 5
#define GPIO_PIN_FUNCTION_G 6
#define GPIO_PIN_FUNCTION_H 7

#define OP1 GPIO(GPIO_PORTA, 4)
#define OP2 GPIO(GPIO_PORTA, 5)
#define ON2 GPIO(GPIO_PORTA, 6)
#define ON1 GPIO(GPIO_PORTA, 7)
#define SCL GPIO(GPIO_PORTA, 8)
#define SDA GPIO(GPIO_PORTA, 9)

#endif // ATMEL_START_PINS_H_INCLUDED

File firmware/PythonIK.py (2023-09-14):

from unittest import skip
import numpy as np # Scientific computing library
import math
import time
import SerialDevice as sd
from matplotlib import pyplot as plt
# from PyQt5.QtWidgets import QApplication, QWidget

"""
GROUND - J0 - J1 - J2 - J3 - J4 - EFFECTOR (trainer)

COORDINATES (TOP DOWN VIEW)
Z+ is up duh

    ^ y+
    |
    |
    0  --> +x

ZERO POSITION
J0 - facing Y+
J1 - parallel to ground facing Y+
J2 - straight
J3 - straight
J4 - doesn't matter lol
J5 - working on it
   o - o - o - | - _ - x  
  _|_
___|___
 / / /

"""

samplerate_hz = 15

class pose:
    def __init__(self, positions=None, rotations=None):
        self.position_mm = [0,0,0] if positions is None else positions
        self.rotation_xyz_rad = [0,0,0] if rotations is None else rotations
        self.joint_angles = [0,0,0,0,0,0]

    def apply_limits(self, a_min, a_max):
        new_angles = []
        for j, amin, amax in zip(self.joint_angles, a_min, a_max):
            new_angles.append(max(min(j, amax), amin))
        self.joint_angles = new_angles

class Robot:
    active_axes = ['x','y','z','a','b']
    angles_min_rad = [-3.0, 0.0, 0.0, -1.5, -3.0, -1.5]
    angles_max_rad = [ 3.0, 2.0, 2.0,  1.5,  3.0,  1.5]
    links_mm = [6.0, 140.82, 250.0, 250.0, 83.5, 50.0]
    sdevice = None
    def __init__(self, skip_sd=False):
        if not skip_sd:
            self.sdevice = sd.SerialDevice()
        self.last_pose = pose()
        self.update_pose()
        time.sleep(0.2)

    # Starting with 3 dof-ish
    def solve_ik(self, tar_pose):
        [x, y, z] = tar_pose.position_mm

        # Rotations are in link J3 coordinate frame to make my life easier
        # Start with J0 cuz it's fully defined by x and y only, #ez
        a0 = math.atan2(x, y)

        # Also J4 is just rotation about x
        a4 = tar_pose.rotation_xyz_rad[0]

        # Calculate where J3 needs to be in xyz space
        end_disp_xy = sum(self.links_mm[4:6]) * math.cos(tar_pose.rotation_xyz_rad[1])
        end_disp_z  = sum(self.links_mm[4:6]) * math.sin(tar_pose.rotation_xyz_rad[1])
        j3pos = [x - (end_disp_xy * math.sin(a0)), y - (end_disp_xy * math.cos(a0)), z - end_disp_z]

        if j3pos[2] < 0:
            print("UHOH bad news bears my friend")

        # Finally calculate J1 and J2
        # on [xy, z] plane
        dz = j3pos[2] - sum(self.links_mm[0:2])
        dxy = self.pthg(j3pos[0], j3pos[1])
        dxyz = self.pthg(dxy, dz)
        temp_a1a = math.atan2(dz, dxy)
        temp_a1b = self.cosines_law(self.links_mm[3], self.links_mm[2], dxyz)
        a1 = temp_a1a + temp_a1b
        a2 = math.pi - self.cosines_law(dxyz, self.links_mm[3], self.links_mm[2])
        a3 = a2 - a1 + tar_pose.rotation_xyz_rad[1]

        tar_pose.joint_angles = [a0, a1, a2, a3, a4, 0]
        tar_pose.apply_limits(self.angles_min_rad, self.angles_max_rad)

    def solve_fk(self, tar_pose):
        a = tar_pose.joint_angles
        hinges_xylen_mm = self.links_mm[2]*math.cos(a[1]) + self.links_mm[3]*math.cos(a[1] - a[2]) + (self.links_mm[4]+ self.links_mm[5]) * math.cos(a[1] - a[2] + a[3])
        xpos = hinges_xylen_mm * math.sin(a[0])
        ypos = hinges_xylen_mm * math.cos(a[0])
        zpos = self.links_mm[0] + self.links_mm[1] + self.links_mm[2]*math.sin(a[1]) + self.links_mm[3]*math.sin(a[1] - a[2]) + (self.links_mm[4]+ self.links_mm[5]) * math.sin(a[1] - a[2] + a[3])
        xang = a[4]
        yang = a[1] - a[2] + a[3]
        zang = 0.0
        return [xpos, ypos, zpos], [xang, yang, zang]

    def update_pose(self):
        positions, angles = self.solve_fk(self.last_pose)
        self.last_pose.position_mm = positions
        self.last_pose.rotation_xyz_rad = angles

    def moveto(self, newpose, velocity, acceleration=0):
        # Calculate moves
        def euclidian_dist(pt1, pt2):
            return pow(pow(pt1[0] - pt2[0], 2) + pow(pt1[1] - pt2[1], 2) + pow(pt1[2] - pt2[2], 2), 0.5)
        vec_len_mm = euclidian_dist(self.last_pose.position_mm, newpose.position_mm)
        steps = int((vec_len_mm / velocity) * samplerate_hz)
        position_vecs = [np.linspace(p0, p1, steps) for p0, p1 in zip(self.last_pose.position_mm, newpose.position_mm)]
        rotation_vecs = [np.linspace(p0, p1, steps) for p0, p1 in zip(self.last_pose.rotation_xyz_rad, newpose.rotation_xyz_rad)]
        def generate_pose(i):
            tp = pose([p[i] for p in position_vecs], [r[i] for r in rotation_vecs])
            self.solve_ik(tp)
            if self.test_pose(tp) is False:
                print("ERRA")
            return tp
        pose_steps = [generate_pose(i) for i in range(steps)]
        
        # Execute moves
        tNext = time.time() + (1 / samplerate_hz)
        for p in pose_steps:
            self.cmd_position(p.joint_angles)
            self.last_pose.joint_angles = p.joint_angles

            if time.time() > tNext: print("UHOH slow down please")
            while(time.time() < tNext): pass
            tNext += (1 / samplerate_hz)

        # Update last pose
        self.update_pose()

    def zero(self):
        cmd = 'g92'
        for ax in self.active_axes:
            cmd += " {}".format(ax)
        # print(cmd)
        self.sdevice.command(cmd)

    def pose_command(self, angles, feedrate=None):
        self.last_pose.joint_angles = angles
        self.update_pose()
        cmd = 'g1'
        for ax, pos in zip(self.active_axes, angles):
            cmd += " {}{}".format(ax, pos)
        if feedrate is not None:
            cmd += " f{}".format(feedrate)
        self.sdevice.command(cmd)

    def cmd_position(self, angles):
        cmd = 'g0'
        for ax, pos in zip(self.active_axes, angles):
            cmd += " {}{}".format(ax, pos)
        self.sdevice.command(cmd)

    def go_home(self):
        self.sdevice.command("g0 z0")
        cmd = 'g0'
        for ax in self.active_axes:
            cmd += " {}0".format(ax)
        self.sdevice.command(cmd)

    def test_pose(self, tar_pose):
        xyz_fw, thetaxyz_fw = self.solve_fk(tar_pose)
        errors_pos = [abs(fw - nm) for fw, nm in zip(xyz_fw, tar_pose.position_mm)]
        errors_ang = [abs(fw - nm) for fw, nm in zip(thetaxyz_fw, tar_pose.rotation_xyz_rad)]

        if (sum(errors_pos) + sum(errors_ang)) > 0.1:
            print("POSITION ERRORS: ", errors_pos)
            print("ANGULAR ERRORS: ", errors_ang)
            return False
        return True

    def pthg(self, x, y):
        return pow(pow(x, 2) + pow(y, 2), 0.5)

    def cosines_law(self, a, b, c):
        # Solve for angle A
        numsum = (-pow(a, 2) + pow(b, 2) + pow(c, 2)) / (2 * b * c)
        numsum = max(min(numsum, 1), -1)
        return math.acos(numsum)

# def plot_robot(tar_pose):
#     points = [[0,0,0]]
#     points.append([0, 0, 0 + links_mm[0]])
#     points.append([0, 0, 0 + sum(links_mm[0:2])])
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

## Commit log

2021-04-11 initial push
    [608 bearing.0003.ipt, 608 bearing.ipt, 6807 bearing.ipt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]
2021-04-25 mostly finish up 75mm harmonic drive, remove deprecated 100mm version
    [AXK100135 thrust bearing.ipt, AXK4060 thrust bearing.0001.ipt, AXK4060 thrust bearing.ipt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]
2021-05-02 HD75mm updates
    [608 bearing.0003.ipt, 608 bearing.ipt, 6815 bearing.0002.ipt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]
2021-05-30 version bump and add 0635mm motor shaft wave generator
    [CF Tube 8x10x250.0002.ipt, CF Tube 8x10x250.ipt, DraftAssembly.0034.iam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]
2021-05-31 upload assembly step file
    [HarmonicDrive75mm.0070.iam, HarmonicDrive75mm.iam]
2021-06-12 ive been busy - significant work on joints 0 and 1 of the arm
    [40mmFan.0001.ipt, 40mmFan.ipt, 6810 bearing.0001.ipt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]
2021-06-15 more cad work, fine tune design and some DFA
    [40mmFan.0001.ipt, 40mmFan.0002.ipt, 40mmFan.ipt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]
2021-07-12 all the updates before the video release
    [Base.0018.ipt, Base.0019.ipt, Base.ipt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]
2021-08-01 add step file
    [DraftAssembly.0115.iam, DraftAssembly.0116.iam, DraftAssembly.iam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]
2021-12-02 continued work on arm, polish up harmonic drive v2
    [AXK6085 thrust bearing.0004.ipt, AXK6085 thrust bearing.0005.ipt, AXK6085 thrust bearing.ipt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]
2021-12-05 continued work on arm, fix harmonic drive file naming
    [DraftAssembly.0134.iam, DraftAssembly.0135.iam, DraftAssembly.iam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]
2022-03-01 update harmonic drive v2 and some work on arm
    [DraftAssembly.0135.iam, DraftAssembly.0139.iam, DraftAssembly.iam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]
2022-08-31 a ridiculous amount of updates that im only now pushing :)
    [685 bearing.0001.ipt, 685 bearing.ipt, DraftAssembly.0139.iam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]
2022-09-26 push everything
    [BaseWasher.0001.ipt, BaseWasher.ipt, BaseWasher.stl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]
